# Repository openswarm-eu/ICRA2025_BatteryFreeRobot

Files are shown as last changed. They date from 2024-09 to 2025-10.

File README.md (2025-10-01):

# ICRA2025_Battery-Free Robot CapBot 

## Abstract

> Swarm robotics focuses on designing and coordinating large groups of relatively simple robots to perform tasks in a decentralised and collective manner.
> The swarm provides a resilient and flexible solution for many applications.
> However, contemporary swarm robots have a significant power problem in that secondary (i.e. rechargeable) batteries are slow to charge and offer lifetimes of only a few years, increasing maintenance costs and pollution due to battery replacement.
> We imagine a different future, wherein battery-free robots powered by supercapacitors can be recharged in seconds, offer long-life autonomous operation and can rapidly pass charge between one another using trophallaxis.
> In pursuit of this vision, we contribute the _CapBot_, a battery-free swarm robot equipped with Mecanum wheels, a Cortex-M4F application processor and Bluetooth Low Energy networking.
> CapBot  fully recharges in 16 s, offers 51 min of autonomous operation at top speed, and can transfer up to 50% of its available charge to a peer via trophallaxis in under 20 s.
> It is fully open-source: all software and hardware sources are available in this repository.

## Artefacts

### Hardware

CapBot's hardware is designed using KiCad, the design files are provided under [Hardware_Design](./Hardware_Design).

### Software

The [Software_Design](./Software_Design) folder contains an example using the CapBot Zephyr API.
The library itself is hosted at our [GitLab instance](https://gitlab.kuleuven.be/distrinet/taskforces/nes/capbot) and is included in this example using git submodules.

# CapBot ICRA demo

Fetch submodules:
```sh
git submodule update --init
```
Open workspace in [Visual Studio Code](https://code.visualstudio.com/):
```sh
code Software_Design
```
Make sure that the nRF Connect extension is installed according to the instructions at [Nordic's DevAcademy](https://academy.nordicsemi.com/courses/nrf-connect-sdk-fundamentals/lessons/lesson-1-nrf-connect-sdk-introduction/topic/exercise-1-1/)
Now, you should be able to open an nRF Connect terminal in Visual Studio Code. 
Next, execute [west](https://docs.nordicsemi.com/bundle/ncs-latest/page/zephyr/develop/west/index.html):
```sh
west build --build-dir build --board freebot-nrf52840 . -- -DBOARD_ROOT=.
```
This builds the demo project and creates a binary at `build/zephyr/zephyr.elf`.
[PyOCD](https://pyocd.io/) can then be used to flash the binary to the robot:
```sh
pyocd load -t nrf52840 build/zephyr/zephyr.hex
```

# Acknowledgement

Part of the source code in this repository is developed within the frame and for the purpose of the OpenSwarm project. This project has received funding from the European Unioan's Horizon Europe Framework Programme under Grant Agreement No. 101093046.

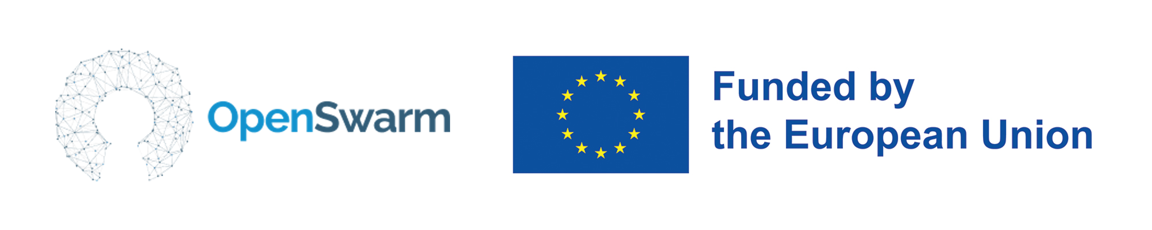
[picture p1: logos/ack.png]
OpenSwarm - Funded by the European Union


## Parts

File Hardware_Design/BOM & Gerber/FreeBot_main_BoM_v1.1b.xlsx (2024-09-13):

FreeBot_BoM
Source: | /Users/fan/work/projects/NetBot/FreeBot/FreeBot_v1.1/FreeBot_main/FreeBot_main_v1.1.kicad_sch
Date: | 2024 March 30, Tuesday 18:43:59
Tool: | Eeschema 7.0.5-0
Generator: | /Applications/KiCad/KiCad.app/Contents/SharedSupport/plugins/bom_csv_grouped_by_value_with_fp.py
Component Count: | 133
Ref | Qnty | Value | Part Nr | Footprint | Description | Vendor
A2 | 0 | DNP | Board layout | Arduino Nano
A3 | 0 | DNP | Board layout | Adafruit Feather
BT1 | 0 | DNP | Battery_Cell | Battery:BatteryHolder_Keystone_1058_1x2032 | Single-cell battery
C1, C24, C32, C33, C37 | 5 | 10uF | C | Capacitor_SMD:C_0603_1608Metric | Unpolarized capacitor
C2, C25, C38 | 3 | 10pF | C | Capacitor_SMD:C_0402_1005Metric | Unpolarized capacitor
C3, C4, C5, C20 | 4 | 1uF | C | Capacitor_SMD:C_0402_1005Metric | Unpolarized capacitor
C6, C8 | 2 | 22p | C | Capacitor_SMD:C_0402_1005Metric | Unpolarized capacitor
C7, C9, C10, C11, C12, C21, C22, C23, C29, C34, C35, C36 | 12 | 0.1uF | C | Capacitor_SMD:C_0402_1005Metric | Unpolarized capacitor
C13, C14, C17, C18, C26, C27, C39, C40 | 8 | 22uF | C | Capacitor_SMD:C_0603_1608Metric | Unpolarized capacitor
C15, C16 | 2 | 12pF | C | Capacitor_SMD:C_0402_1005Metric | Unpolarized capacitor
C19 | 1 | 2.2uF | C | Capacitor_SMD:C_0402_1005Metric | Unpolarized capacitor
C28 | 1 | 0.01uF | C | Capacitor_SMD:C_0402_1005Metric | Unpolarized capacitor
C30 | 0 | DNP | C | Capacitor_SMD:C_0603_1608Metric | Unpolarized capacitor
C31 | 0 | DNP | C | Capacitor_SMD:C_0402_1005Metric | Unpolarized capacitor
D1 | 1 | LED Red | NCD0603R1 | LED_SMD:LED_0603_1608Metric | Light emitting diode
D2 | 1 | LED Green | NCD0603G1 | LED_SMD:LED_0603_1608Metric | Light emitting diode
D3, D6, D17 | 3 | CUS10S30,H3F | 1N4148WS | Diode_SMD:D_SOD-323 | 75V 0.15A Fast switching Diode, SOD-323
D4, D5 | 2 | Schottky Rectifier Low VF Low IR | 10S45SP | Package_TO_SOT_SMD:TO-277A | 600V 6.0A Ultrafast Rectifier, TO-277A
D7, D10, D11, D14 | 0 | DNP | LED | LED_SMD:LED_0603_1608Metric | Light emitting diode
D8, D9, D12, D13 | 0 | DNP | LED | LED_SMD:LED_0603_1608Metric | Light emitting diode
D15, D16 | 2 | LED Blue | 19-217/BHC-ZL1M2RY/3T | LED_SMD:LED_0603_1608Metric | Light emitting diode
F1 | 1 | 0467002.NRHF | Fuse | Fuse:Fuse_0603_1608Metric | Fuse
FID1, FID2 | 0 | DNP | Fiducial | Fiducial:Fiducial_1mm_Mask2mm | Fiducial Marker
H1, H2, H3, H4, H5, H6, H7, H8 | 0 | DNP | MountingHole | MountingHole:MountingHole_2.2mm_M2_ISO7380 | Mounting Hole without connection
H9, H10, H11, H12 | 0 | DNP | MountingHole | MountingHole:MountingHole_3.2mm_M3_ISO14580 | Mounting Hole without connection
J1 | 1 | USB TYPE-C 16P | NCD0603G1 | Fan-socket-connector:TYPE-C-31-M-12
J2, J18 | 0 | DNP | Conn_01x05 | Connector_PinHeader_2.54mm:PinHeader_1x05_P2.54mm_Vertical | Generic connector, single row, 01x05, script generated (kicad-library-utils/schlib/autogen/connector/)
J3 | 0 | DNP | Conn_01x04 | Connector_PinHeader_2.54mm:PinHeader_1x04_P2.54mm_Vertical | Generic connector, single row, 01x04, script generated (kicad-library-utils/schlib/autogen/connector/)
J4, J5 | 2 | ROUND SPACER STEEL 2MM | 9774020960R (国产替代） | ROUND SPACER STEEL 2MM | ROUND SPACER STEEL 2MM | https://item.taobao.com/item.htm?_u=t2dmg8j26111&id=614508475805&skuId=4918073876504
J6 | 1 | Barrel_Jack_MountingPin | Barrel_Jack_MountingPin | Connector_BarrelJack:BarrelJack_GCT_DCJ200-10-A_Horizontal | DC Barrel Jack with a mounting pin
J7, J8, J9, J10 | 4 | ZH 1x6p1.5mm | ZH 1.5-6A | Fan-Connectors:ZH-1.5mm-1x6p-TH | Generic connector, single row, 01x06, script generated (kicad-library-utils/schlib/autogen/connector/)
J11 | 0 | DNP | Conn_01x07 | Connector_PinHeader_2.00mm:PinHeader_1x07_P2.00mm_Vertical | Generic connector, single row, 01x07, script generated (kicad-library-utils/schlib/autogen/connector/)
J12 | 0 | DNP | Conn_02x08_Odd_Even | Connector_PinHeader_2.54mm:PinHeader_2x08_P2.54mm_Horizontal | Generic connector, double row, 02x08, odd/even pin numbering scheme (row 1 odd numbers, row 2 even numbers), script generated (kicad-library-utils/schlib/autogen/connector/)
J13 | 0 | DNP | Conn_01x06 | Connector_PinHeader_2.54mm:PinHeader_1x06_P2.54mm_Vertical_SMD_Pin1Right
J14, J16 | 2 | DZ-32 | Conn_01x01 | Fan-Connectors:M3-side-terminal-DZ-32 | Generic connector, single row, 01x01, script generated (kicad-library-utils/schlib/autogen/connector/) | https://item.taobao.com/item.htm?_u=u2im4ruf08aa&id=528747753236&skuId=4568652374504
J15, J17 | 2 | DZ-43 | Conn_01x01 | Fan-Connectors:M3-side-terminal-DZ-43 | Generic connector, single row, 01x01, script generated (kicad-library-utils/schlib/autogen/connector/) | https://item.taobao.com/item.htm?_u=u2im4ruf08aa&id=528747753236&skuId=4568652374504
J19 | 0 | DNP | Conn_01x02 | Connector_PinHeader_2.54mm:PinHeader_1x02_P2.54mm_Vertical | Generic connector, single row, 01x02, script generated (kicad-library-utils/schlib/autogen/connector/)
J21 | 1 | HDGC2001WR-S-2P | Conn_01x03 | Connector_JST:JST_PH_S2B-PH-SM4-TB_1x02-1MP_P2.00mm_Horizontal
J23, J24 | 0 | DNP | Conn_01x08 | Connector_PinHeader_2.54mm:PinHeader_1x08_P2.54mm_Vertical_SMD_Pin1Right
J25 | 0 | DNP | Conn_01x10 | Connector_PinHeader_2.54mm:PinHeader_1x10_P2.54mm_Vertical_SMD_Pin1Right
L1 | 1 | 300nH | FXL1040-R30-M | Inductor_SMD:L_Chilisin_BMRF00101040 | Inductor
L2, L3 | 2 | 470nH | FXL0420-R47-M | Inductor_SMD:L_Sunlord_MWSA0412S | Inductor
L4 | 1 | 1uH | FXL0630-1R0-M | Inductor_SMD:L_Sunlord_MWSA0603S | Inductor
R1, R2 | 2 | 5.1k | R | Resistor_SMD:R_0402_1005Metric | Resistor
R3, R7, R18, R22, R27, R31, R32, R35, R36, R38, R40, R44, R45, R48, R68, R70 | 16 | 100k | R | Resistor_SMD:R_0402_1005Metric | Resistor
R4, R5, R6, R11, R12, R13, R14, R15, R16 | 9 | 22 | R | Resistor_SMD:R_0402_1005Metric | Resistor
R8, R29, R30, R33, R37, R41, R51, R52, R53, R54, R55, R56, R57, R58, R61, R65 | 0 | DNP | R | Resistor_SMD:R_0402_1005Metric | Resistor
R9, R20, R59, R60 | 4 | 100 | R | Resistor_SMD:R_0402_1005Metric | Resistor
R10, R62, R66 | 3 | 0 | R | Resistor_SMD:R_0402_1005Metric | Resistor
R17 | 1 | 1.5k | R | Resistor_SMD:R_0402_1005Metric | Resistor
R19 | 0 | DNP | R | Resistor_SMD:R_1206_3216Metric | Resistor
R21 | 1 | 27 | R | Resistor_SMD:R_0402_1005Metric | Resistor
R23, R25, R43, R47, R50 | 5 | 10k | R | Resistor_SMD:R_0402_1005Metric | Resistor
R24 | 1 | 36.5k | R | Resistor_SMD:R_0402_1005Metric | Resistor
R26, R67 | 2 | 1 | R | Resistor_SMD:R_0402_1005Metric | Resistor
R28 | 1 | 499k | R | Resistor_SMD:R_0402_1005Metric | Resistor
R34 | 1 | 348k | R | Resistor_SMD:R_0402_1005Metric | Resistor
R39 | 1 | 316k | R | Resistor_SMD:R_0402_1005Metric | Resistor
R42, R46, R49 | 3 | 390k | R | Resistor_SMD:R_0402_1005Metric | Resistor
R69 | 1 | 806k | R | Resistor_SMD:R_0402_1005Metric | Resistor
R63, R64 | 0 | DNP | R | Resistor_SMD:R_0805_2012Metric_Pad1.20x1.40mm_HandSolder | Resistor
SW1, SW2 | 2 | SW_Push | TS-1088-AR02016 | Button_Switch_SMD:SW_Push_SPST_NO_Alps_SKRK | Push button switch, generic, two pins
SW3 | 0 | DNP | Switch-4PDT | Fan-switch:4PDT-K3-2268S-F1
SW4 | 0 | DNP | Switch-DPDT | Fan-switch:DPDT-K3-2235S-F1
U1, U11 | 2 | Boost DCDC | TPS61021ADSGR | Package_SON:WSON-8-1EP_2x2mm_P0.5mm_EP0.9x1.6mm_ThermalVias
U2 | 1 | SPDT analog switch | TS5A23159DGSR | Package_SO:VSSOP-10_3x3mm_P0.5mm | Dual SPDT 1ohm Bidirectional Analog Switch with Off protection, VSSOP-10
U3 | 1 | STM32F103CBTx | STM32F103CBT6 | Package_QFP:LQFP-48_7x7mm_P0.5mm | STMicroelectronics Arm Cortex-M3 MCU, 128KB flash, 20KB RAM, 72 MHz, 2.0-3.6V, 37 GPIO, LQFP48
U4, U5, U6, U7 | 4 | Motor-driver-1ch | BDR6120H | Fan-Motor:motor-driver-BDR6120H
U8 | 1 | Buck SIC431 | SIC431BED-T1-GE3 | Fan-pwr:MLP44-24L SiC431
U9 | 1 | RF Module | E73-2G4M08S1C | Fan-MCU-Library:E73-2G4M08S1C
U10, U17 | 0 | DNP | TS5A23159DGSR | Package_SO:VSSOP-10_3x3mm_P0.5mm | Dual SPDT 1ohm Bidirectional Analog Switch with Off protection, VSSOP-10
U12 | 0 | DNP | RT9742AGJ5F | Package_TO_SOT_SMD:TSOT-23-5 | 3A, Discharge, Active High EN, TSOT-23-5
U13 | 1 | 100mA Voltage Regulator | HT7536-1 | Package_TO_SOT_SMD:SOT-89-3 | 100mA Low Dropout Voltage Regulator, Fixed Output, SOT89
U14 | 1 | Boost DCDC | TPS61022RWUR | VQFN7_2x2 | 8-A boost converter with 0.5-V ultra-low input voltage in a VQFN-HR (RWU) package with 7 pins.
U15 | 1 | TS3A27518EPWR | TS3A27518EPW | Package_SO:TSSOP-24_4.4x7.8mm_P0.65mm | 6-channel analog mux, TSSOP-24
Y1 | 1 | Crystal_GND24 | X32258MSB4SI | Crystal:Crystal_SMD_3225-4Pin_3.2x2.5mm | Crystal 8MHz
Y2 | 1 | Crystal | Q13FC1350000400 | Crystal:Crystal_SMD_3215-2Pin_3.2x1.5mm | Crystal 32.768kHz | Q13FC1350000400

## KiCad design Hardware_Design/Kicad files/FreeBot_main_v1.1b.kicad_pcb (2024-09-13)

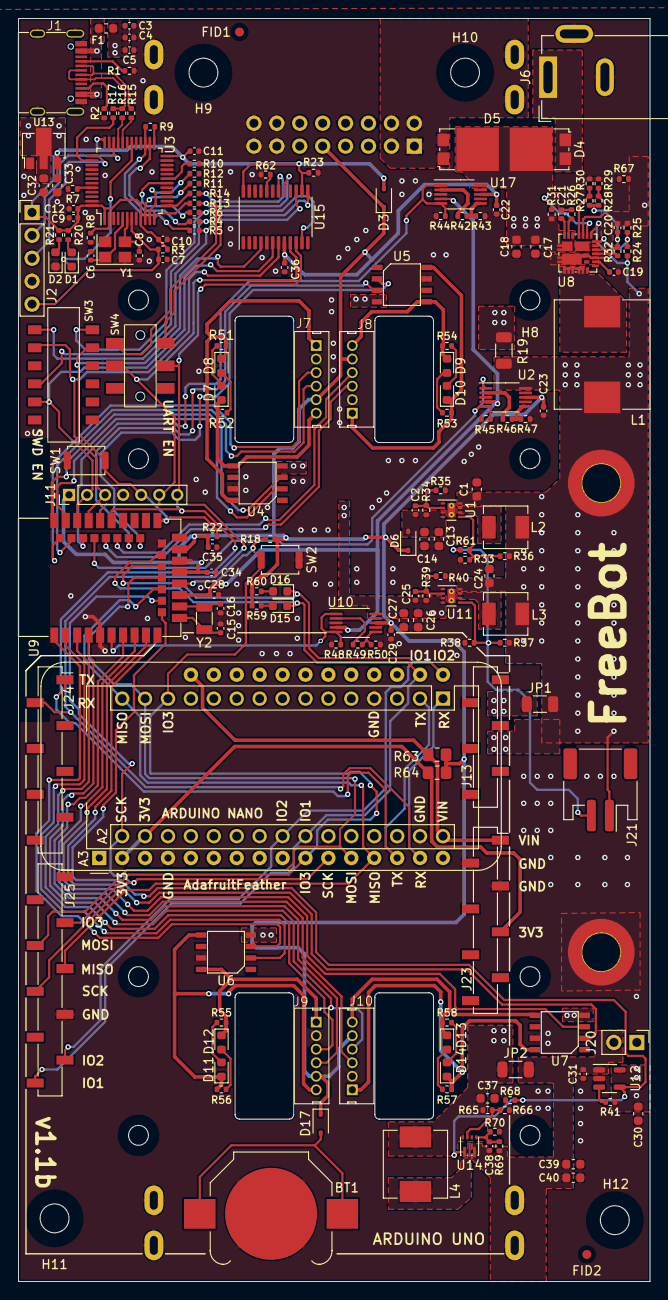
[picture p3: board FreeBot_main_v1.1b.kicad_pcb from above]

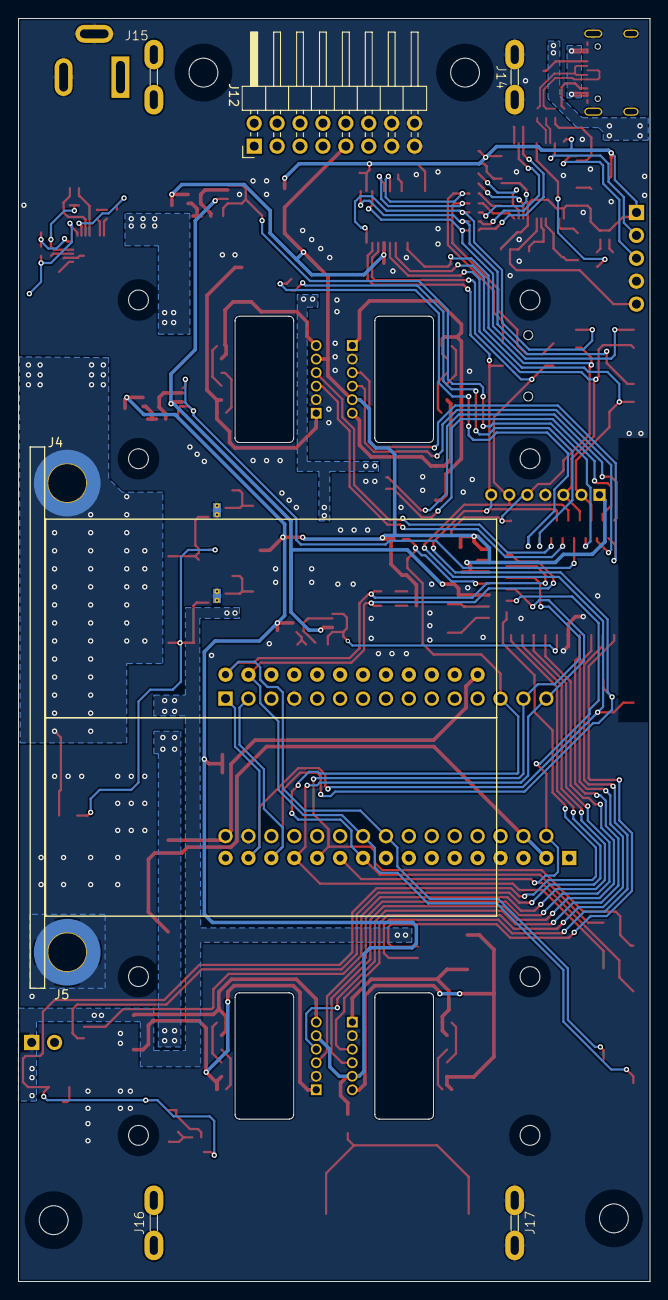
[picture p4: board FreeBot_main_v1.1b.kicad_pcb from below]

Board: 2 copper layers, 70.0 x 140.0 mm, 194 parts (7 on the bottom side), 126 nets.

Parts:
A2: Arduino_Nano_v3.x; Arduino_Nano
A3: Adafruit_Feather_Generic; Adafruit_Feather
BT1: Battery_Cell; BatteryHolder_Keystone_3000_1x12mm
C1, C24, C30, C32, C33, C37: 10uF; C_0603_1608Metric
C2, C25, C38: 10pF; C_0402_1005Metric
C3, C4, C5, C20: 1uF; C_0402_1005Metric
C6, C8: 22p; C_0402_1005Metric
C7, C9, C10, C11, C12, C21, C22, C23, C29, C31, C34, C35, C36: 0.1uF; C_0402_1005Metric
C13, C14, C17, C18, C26, C27, C39, C40: 22uF; C_0603_1608Metric
C15, C16: 12pF; C_0402_1005Metric
C19: 2.2uF; C_0402_1005Metric
C28: 0.01uF; C_0402_1005Metric
D1: Red; LED_0603_1608Metric
D2: Green; LED_0603_1608Metric
D3, D6, D17: CUS10S30,H3F; D_SOD-323
D4, D5: 10S45SP; TO-277A
D7, D10, D11, D14: GREEN LED NCD0603G1; LED_0603_1608Metric
D8, D9, D12, D13: RED LED NCD0603R1; LED_0603_1608Metric
D15, D16: 19-217/BHC-ZL1M2RY/3T; LED_0603_1608Metric
F1: S1206-F-6.0A; Fuse_0603_1608Metric
FID1, FID2: Fiducial; Fiducial_1mm_Mask2mm
H1, H2, H3, H4, H5, H6, H7, H8: MountingHole; MountingHole_2.2mm_M2_ISO7380
H9, H10, H11, H12: MountingHole; MountingHole_3.2mm_M3_ISO14580
J1: USB-type-c-16p; TYPE-C-31-M-12
J2: Conn_01x05; PinHeader_1x05_P2.54mm_Vertical
J4, J5: Conn_01x01; MountingHole_3.2mm_M3_Pad_TopBottom
J6: Barrel_Jack_MountingPin; BarrelJack_GCT_DCJ200-10-A_Horizontal
J7, J8, J9, J10: Conn_01x06; ZH-1.5mm-1x6p-TH
J11: Conn_01x07; PinHeader_1x07_P2.00mm_Vertical
J12: Conn_02x08_Odd_Even; PinHeader_2x08_P2.54mm_Horizontal
J13: Conn_01x06; PinSocket_1x06_P2.54mm_Vertical_SMD_Pin1Right
J14, J16: Conn_01x01; M3-side-terminal-DZ-32
J15, J17: Conn_01x01; M3-side-terminal-DZ-43
J20: Conn_01x02; PinHeader_1x02_P2.54mm_Vertical
J21: Conn_01x02; JST_PH_S2B-PH-SM4-TB_1x02-1MP_P2.00mm_Horizontal
J23, J24: Conn_01x08; PinSocket_1x08_P2.54mm_Vertical_SMD_Pin1Right
J25: Conn_01x10; PinSocket_1x10_P2.54mm_Vertical_SMD_Pin1Right
JP1, JP2: SolderJumper_2_Open; R_1206_3216Metric
L1: 300nH; L_Chilisin_BMRF00101040
L2, L3: 470nH FXL0420-R47-M; L_Sunlord_MWSA0412S
L4: 1uH FXL0630-1R0-M; L_Sunlord_MWSA0603S
R1, R2: 5.1k; R_0402_1005Metric
R3, R7, R18, R22, R27, R31, R32, R35, R36, R38, R40, R41, R44, R45, R48, R68, R70: 100k; R_0402_1005Metric
R4, R5, R6, R11, R12, R13, R14, R15, R16: 22; R_0402_1005Metric
R8: 10k DNP; R_0402_1005Metric
R9, R20, R52, R53, R56, R57, R59, R60: 100; R_0402_1005Metric
R10, R62, R66: 0; R_0402_1005Metric
R17: 1.5k; R_0402_1005Metric
R19: DNP; R_1206_3216Metric
R21, R51, R54, R55, R58: 27; R_0402_1005Metric
R23, R25, R43, R47, R50: 10k; R_0402_1005Metric
R24: 36.5k; R_0402_1005Metric
R26, R67: 1; R_0402_1005Metric
R28: 499k; R_0402_1005Metric
R29, R30, R33, R37, R61, R65: DNP; R_0402_1005Metric
R34: 348k; R_0402_1005Metric
R39: 316k; R_0402_1005Metric
R42, R46, R49: 390k; R_0402_1005Metric
R63, R64: R; R_0805_2012Metric_Pad1.20x1.40mm_HandSolder
R69: 806k; R_0402_1005Metric
SW1, SW2: TS-1088-AR02016; SW_Push_SPST_NO_Alps_SKRK
SW3: 4PDT-K3-2268S-F1
SW4: Switch-DPDT; DPDT-K3-2235S-F1
U1, U11: WSON-8-1EP_2x2mm_P0.5mm_EP0.9x1.6mm_ThermalVias
U2, U10, U17: TS5A23159DGS; VSSOP-10_3x3mm_P0.5mm
U3: STM32F103CBTx; LQFP-48_7x7mm_P0.5mm
U4, U5, U6, U7: BDR6120H; motor-driver-BDR6120H
U8: SIC431AED-T1-GE3; MLP44-24L SiC431
U9: E73-2G4M08S1C
U12: RT9742AGJ5F; TSOT-23-5
U13: HT7536-1; SOT-89-3
U14: boost-TPS61022; VQFN-HR-7 TPS61022
U15: TS3A27518EPW; TSSOP-24_4.4x7.8mm_P0.65mm
Y1: Crystal_GND24; Crystal_SMD_3225-4Pin_3.2x2.5mm
Y2: Q13FC1350000400; Crystal_SMD_3215-2Pin_3.2x1.5mm

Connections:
/USB-VDD: C9.1, C10.1, C11.1, C12.1, C33.1, D3.2 (A), J2.1, R3.2, R20.1, R21.1, R23.1, U3.1 (VBAT), U3.9 (VDDA), U3.24 (VDD), U3.36 (VDD), U3.48 (VDD), U13.3 (VOUT), U15.14 (IN2), U15.24 (IN1)
/Vbotin: D5.1 (A), D5.2 (A), J12.1, J12.2, J12.3, J12.4, J15.1
/Vbotout: C31.2, C38.2, C39.1, C40.1, J16.1, J20.2, JP2.2 (B), R69.1, U12.1 (VOUT), U14.3 (VOUT)
/Vmotor: C25.2, C26.1, C27.1, C30.1, J20.1, JP1.2 (B), R39.1, R41.1, U4.4 (VDD), U5.4 (VDD), U6.4 (VDD), U7.4 (VDD), U10.10, U11.3 (VOUT), U11.4 (VOUT), U12.5 (VIN)
/add-on-board/3V3: A2.17 (3V3), A3.2 (3V3), J23.5, R64.2
/add-on-board/VIN: A2.30 (VIN), A3.28 (VBAT), J23.1, R63.2
/add-on-board/addon-io.1: A2.24 (A5), A3.18 (SCL), D15.1 (K), J25.10, U9.22 (P0.07)
/add-on-board/addon-io.2: A2.23 (A4), A3.17 (SDA), D16.1 (K), J25.9, U9.20 (P0.12)
/add-on-board/addon-io.3: A2.13 (D10), A3.10 (A5), J25.3, R18.2, SW2.2, U9.17 (P1.09)
/add-on-board/addon-spi.miso: A2.15 (D12), A3.13 (MISO), J25.5, U9.16 (P0.08)
/add-on-board/addon-spi.mosi: A2.14 (D11), A3.12 (MOSI), J25.4, U9.18 (P0.04/AIN2)
/add-on-board/addon-spi.sck: A2.16 (D13), A3.11 (SCK), J25.6, U9.14 (P0.06)
/add-on-board/uart.rx: A2.1 (D1/TX), A3.15 (TX), J11.6, J24.2, SW4.5, U9.35 (P0.24), U15.9 (COM4)
/add-on-board/uart.tx: A2.2 (D0/RX), A3.14 (RX), J11.7, J24.1, SW4.2, U9.33 (P0.13), U15.10 (COM5)
/daplink/dap-inner-usb_N: R15.2, U3.32 (PA11)
/daplink/dap-inner-usb_P: R16.2, U3.33 (PA12)
/daplink/dap-led-red: D1.1 (K), U3.30 (PA9)
/daplink/dap-nrst: C7.1, J2.5, R3.1, U3.7 (NRST)
/daplink/dap-swclk: J2.3, U3.37 (PA14)
/daplink/dap-swdio: J2.2, U3.34 (PA13)
/daplink/dap-usbd_N: J1.A7 (DN1), J1.B7 (DN2), R15.1
/daplink/dap-usbd_P: J1.A6 (DP1), J1.B6 (DP2), R16.1, R17.2
/daplink/tgt-rx-dap: R13.2, SW4.4, U15.17 (NO4)
/daplink/tgt-swd-clk-dap: R4.1, SW3.10, U15.13 (NO2)
/daplink/tgt-swd-io-dap: R5.1, SW3.7, U15.15 (NO3)
/daplink/tgt-swd-rst-dap: R6.1, SW3.1, U15.11 (NO1)
/daplink/tgt-swd.clk: J11.2, SW3.11, U9.39 (SWDCLK), U15.6 (COM2)
/daplink/tgt-swd.io: J11.3, SW3.8, U9.37 (SWDIO), U15.7 (COM3)
/daplink/tgt-swd.rst: J11.5, R22.2, SW1.2, SW3.2, U9.26 (P0.18/RESET), U15.4 (COM1)
/daplink/tgt-tx-dap: R14.2, SW4.1, U15.18 (NO5)
/mcu/V-mea: C28.1, U2.4, U9.15 (P0.05/AIN3), U10.4, U17.4
/mcu/Vbotout-EN: R68.1, U9.12 (P0.26), U12.4 (EN), U14.1 (EN)
/mcu/Vcap-mea-en: R45.1, U2.1, U2.5, U9.36 (P1.00/SWO)
/mcu/Vin-mea-en: R44.1, U9.38 (P1.02-LS), U17.1, U17.5
/mcu/Vmotor-mea-en: R48.1, U9.6 (P1.13-LS), U10.1, U10.5
/mcu/m1-ctrl.in-a: U4.2 (INA), U9.41 (P0.09/NFC1-LS)
/mcu/m1-ctrl.in-b: U4.3 (INB), U9.43 (P0.10/NFC2-LS)
/mcu/m1-hall.c1: J7.4, U9.40 (P1.04-LS)
/mcu/m1-hall.c2: J7.3, U9.42 (P1.06-LS)
/mcu/m2-ctrl.in-a: U5.2 (INA), U9.28 (P0.15)
/mcu/m2-ctrl.in-b: U5.3 (INB), U9.30 (P0.17)
/mcu/m2-hall.c1: J8.4, U9.32 (P0.20)
/mcu/m2-hall.c2: J8.3, U9.34 (P0.22)
/mcu/m3-ctrl.in-a: U6.2 (INA), U9.2 (P1.10-LS)
/mcu/m3-ctrl.in-b: U6.3 (INB), U9.1 (P1.11-LS)
/mcu/m3-hall.c1: J9.4, U9.7 (P0.02/AIN1-LS)
/mcu/m3-hall.c2: J9.3, U9.3 (P0.03/AIN1-LS)
/mcu/m4-ctrl.in-a: U7.2 (INA), U9.10 (P0.30/AIN6-LS)
/mcu/m4-ctrl.in-b: U7.3 (INB), U9.9 (P0.31/AIN7-LS)
/mcu/m4-hall.c1: J10.4, U9.4 (P0.28/AIN4-LS)
/mcu/m4-hall.c2: J10.3, U9.8 (P0.29/AIN5-LS)
/pwr1/buck_en: R31.2, U8.19 (EN)
/pwr2/Vbotout-overcurr: R41.2, U12.3 (~FLG)
/pwr2/Vcap: C1.1, C24.1, C37.1, J4.1, J21.1, JP1.1 (A), JP2.1 (A), L1.2, L2.1, L3.1, L4.1, R19.2, R24.1, R36.1, R37.1, R65.1, U1.8 (VIN), U2.10, U8.18 (Vout), U11.8 (VIN), U14.7 (VIN)
/pwr2/Vcap_reg: C2.2, C13.1, C14.1, D6.2 (A), R34.1, U1.3 (VOUT), U1.4 (VOUT)
/pwr2/Vmotor-EN: J21.2, R37.2, R38.1, R61.2, U11.5 (EN)
GND: A2.4 (GND), A2.29 (GND), A3.4 (GND), BT1.2 (-), C1.2, C3.2, C4.2, C5.2, C6.2, C7.2, C8.2, C9.2, C10.2, C11.2, C12.2, C13.2, C14.2, C15.2, C16.2, C17.2, C18.2, C19.2, C20.2, C22.2, C23.2, C24.2, C26.2, C27.2, C28.2, C29.2, C30.2, C31.1, C32.2, C33.2, C34.2, C35.2, C36.1, C37.2, C39.2, C40.2, D2.1 (K), J1.0 (SH), J1.1 (SH), J1.2 (SH), J1.3 (SH), J1.A1 (GND), J1.A12 (GND), J1.B1 (GND), J1.B12 (GND), J2.4, J5.1, J6.2, J6.3 (MP), J7.2, J8.2, J9.2, J10.2, J11.4, J12.13, J12.14, J12.15, J12.16, J14.1, J17.1, J23.2, J23.3, J25.7, R1.2, R2.2, R7.2, R8.1, R10.1, R23.2, R25.2, R29.2, R30.2, R33.2, R35.2, R38.2, R40.2, R43.2, R44.2, R45.2, R47.2, R48.2, R50.2, R62.1, R66.2, R67.1, R67.2, R68.2, R70.2, SW1.1, SW2.1, U1.1 (AGND), U1.9 (PGND), U2.3 (GND), U3.8 (VSSA), U3.23 (VSS), U3.35 (VSS), U3.47 (VSS), U4.7 (GND), U5.7 (GND), U6.7 (GND), U7.7 (GND), U8.3 (Pgnd), U8.4 (Pgnd), U8.13 (Pgnd), U8.16 (Agnd), U8.25 (Agnd), U8.27 (Pgnd), U9.5 (GND), U9.21 (GND), U9.24 (GND), U10.3 (GND), U11.1 (AGND), U11.9 (PGND), U12.2 (GND), U13.1 (GND), U15.5 (GND), U17.3 (GND), Y1.2, Y1.4
unnamed: BT1.1 (+), D17.2 (A)
unnamed: C21.2, R26.2
unnamed: D1.2 (A), R20.2
unnamed: D2.2 (A), R21.2
unnamed: D4.1 (A), D4.2 (A), J6.1
unnamed: C17.1, C18.1, D4.3 (K), D5.3 (K), R19.1, R31.1, U8.1 (Vin), U8.2 (Vin), U8.22 (Vin), U8.26 (Vin), U17.10
unnamed: D7.2 (A), R51.2
unnamed: D7.1 (K), J7.6, R52.2, U4.5 (OUTB)
unnamed: D8.2 (A), R52.1
unnamed: D8.1 (K), J7.1, R51.1, U4.8 (OUTA)
unnamed: D9.2 (A), R53.2
unnamed: D9.1 (K), J8.6, R54.2, U5.5 (OUTB)
unnamed: D10.2 (A), R54.1
unnamed: D10.1 (K), J8.1, R53.1, U5.8 (OUTA)
unnamed: D11.2 (A), R55.2
unnamed: D11.1 (K), J9.6, R56.2, U6.5 (OUTB)
unnamed: D12.2 (A), R56.1
unnamed: D12.1 (K), J9.1, R55.1, U6.8 (OUTA)
unnamed: D13.2 (A), R57.2
unnamed: D13.1 (K), J10.6, R58.2, U7.5 (OUTB)
unnamed: D14.2 (A), R58.1
unnamed: D14.1 (K), J10.1, R57.1, U7.8 (OUTA)
unnamed: D15.2 (A), R59.2
unnamed: D16.2 (A), R60.2
unnamed: F1.1, J1.A4 (VBUS), J1.A9 (VBUS), J1.B4 (VBUS), J1.B9 (VBUS)
unnamed: J1.A5 (CC1), R1.1
unnamed: J1.B5 (CC2), R2.1
unnamed: L1.1, U8.5 (SW), U8.6 (SW), U8.7 (SW), U8.8 (SW), U8.9 (SW)
unnamed: L2.2, U1.6 (SW), U1.7 (SW)
unnamed: L3.2, U11.6 (SW), U11.7 (SW)
unnamed: R42.1, U17.2
unnamed: R42.2, R43.1, U17.6
unnamed: R46.1, U2.2
unnamed: R46.2, R47.1, U2.6
unnamed: R49.1, U10.2
unnamed: R49.2, R50.1, U10.6
unnamed: R33.1, R36.2, R61.1, U1.5 (EN)
unnamed: C2.1, R34.2, R35.1, U1.2 (FB)
unnamed: R7.1, U3.44 (BOOT0)
unnamed: R11.1, U3.10 (PA0)
unnamed: R12.1, U3.11 (PA1)
unnamed: R13.1, U3.12 (PA2)
unnamed: R14.1, U3.13 (PA3)
unnamed: R17.1, U3.38 (PA15)
unnamed: R6.2, U3.18 (PB0)
unnamed: R10.2, U3.19 (PB1)
unnamed: R9.2, U3.25 (PB12)
unnamed: R4.2, U3.26 (PB13)
unnamed: R5.2, R9.1, U3.27 (PB14)
unnamed: R8.2, U3.2 (PC13)
unnamed: C6.1, U3.5 (PD0), Y1.1
unnamed: C8.1, U3.6 (PD1), Y1.3
unnamed: R26.1, U8.23 (BOOT)
unnamed: R24.2, R25.1, U8.17 (FB)
unnamed: R27.2, R30.1, U8.21 (MODE1)
unnamed: R28.2, R29.1, U8.20 (MODE2)
unnamed: C21.1, U8.24 (PHASE)
unnamed: R32.2, U8.14 (Pgood)
unnamed: C20.1, R27.1, R28.1, R32.1, U8.15 (Vdd)
unnamed: C19.1, U8.12 (Vdrv)
unnamed: C15.1, U9.11 (P0.00/XL1), Y2.1
unnamed: C16.1, U9.13 (P0.01/XL2), Y2.2
unnamed: C25.1, R39.2, R40.1, U11.2 (FB)
unnamed: C38.1, R69.2, R70.1, U14.4 (FB)
unnamed: R65.2, R66.1, U14.6 (MODE)
unnamed: L4.2, U14.2 (SW)
unnamed: R62.2, U15.20 (~EN)
VBUS: C3.1, C4.1, C5.1, C32.1, F1.2, U13.2 (VIN)
VDD: C22.1, C23.1, C29.1, C34.1, C35.1, C36.2, D3.1 (K), D6.1 (K), D17.1 (K), J7.5, J8.5, J9.5, J10.5, J11.1, J12.9, R18.1, R22.1, R59.1, R60.1, R63.1, R64.1, U2.8 (VCC), U9.19 (VDD), U9.23 (VDDH), U10.8 (VCC), U15.8 (VCC), U17.8 (VCC)

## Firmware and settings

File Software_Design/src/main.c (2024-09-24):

/**
 * @file main.c
 * @author Lowie Deferme <lowie.deferme@kuleuven.be>
 * @brief FreeBot zephyr example
 * @version 0.1
 * @date 2024-09-22
 *
 * @copyright Copyright (c) 2024
 *
 */

#include <zephyr/kernel.h>
#include <zephyr/logging/log.h>

LOG_MODULE_REGISTER(demo, LOG_LEVEL_DBG);

#include "freebot.h"
#define FB_DEMO_DELAY K_MSEC(500)
#define FB_DEMO_SPEED 75

static fb_motor_angle_t motor_angles;
static fb_motor_speed_t motor_speeds;

void pwr_measure_demo(void)
{
    fb_v_measure_select(V_CAP);
    k_sleep(FB_DEMO_DELAY);
    int v_cap = fb_v_measure();
    LOG_DBG("Vcap = %dmV", v_cap);
}

void motor_drive_demo(void)
{
    fb_straight_forw(FB_DEMO_SPEED);
    LOG_DBG("Robot going forward");
    k_sleep(FB_DEMO_DELAY);

    fb_straight_back(FB_DEMO_SPEED);
    LOG_DBG("Robot going backward");
    k_sleep(FB_DEMO_DELAY);

    fb_side_right(FB_DEMO_SPEED);
    LOG_DBG("Robot going right");
    k_sleep(FB_DEMO_DELAY);

    fb_side_left(FB_DEMO_SPEED);
    LOG_DBG("Robot going left");
    k_sleep(FB_DEMO_DELAY);

    fb_side_d45(FB_DEMO_SPEED);
    LOG_DBG("Robot going 45°");
    k_sleep(FB_DEMO_DELAY);

    fb_side_d135(FB_DEMO_SPEED);
    LOG_DBG("Robot going 135°");
    k_sleep(FB_DEMO_DELAY);

    fb_side_d225(FB_DEMO_SPEED);
    LOG_DBG("Robot going 225°");
    k_sleep(FB_DEMO_DELAY);

    fb_side_d315(FB_DEMO_SPEED);
    LOG_DBG("Robot going 315°");
    k_sleep(FB_DEMO_DELAY);

    fb_rotate_cw(FB_DEMO_SPEED);
    LOG_DBG("Robot rotating clockwise");
    k_sleep(FB_DEMO_DELAY);

    fb_rotate_ccw(FB_DEMO_SPEED);
    LOG_DBG("Robot rotating counterclockwise");
    k_sleep(FB_DEMO_DELAY);

    fb_stop();
    LOG_DBG("Robot stopped");
}

void motor_measure_demo(void)
{
    fb_get_motor_angle(&motor_angles);
    LOG_DBG("{%d°, %d°, %d°, %d°}", motor_angles.front_left, motor_angles.front_right,
            motor_angles.back_left, motor_angles.back_right);

    fb_rotate_cw(FB_DEMO_SPEED);
    k_sleep(K_MSEC(200));
    fb_get_motor_speed(&motor_speeds);
    LOG_DBG("{%d rpm, %d rpm, %d rpm, %d rpm}", motor_speeds.front_left, motor_speeds.front_right,
            motor_speeds.back_left, motor_speeds.back_right);

    fb_stop();
    for (int i = 0; i < 4; i++)
    {
        k_sleep(K_MSEC(100));
        fb_get_motor_speed(&motor_speeds);
        LOG_DBG("{%d rpm, %d rpm, %d rpm, %d rpm}", motor_speeds.front_left,
                motor_speeds.front_right, motor_speeds.back_left, motor_speeds.back_right);
    }

    fb_get_motor_angle(&motor_angles);
    LOG_DBG("{%d°, %d°, %d°, %d°}", motor_angles.front_left, motor_angles.front_right,
            motor_angles.back_left, motor_angles.back_right);
}

void motor_speed_demo(void)
{
    const int STEPS = 10;
    for (int i = 0; i <= STEPS; i++)
    {
        fb_rotate_cw(100 * i / STEPS);
        LOG_DBG("Target speed: %d", 100 * i / STEPS);
        for (int j = 0; j < 10; j++)
        {
            k_sleep(K_MSEC(100));
            fb_get_motor_speed(&motor_speeds);
            LOG_DBG("{%d rpm, %d rpm, %d rpm, %d rpm}", motor_speeds.front_left,
                    motor_speeds.front_right, motor_speeds.back_left, motor_speeds.back_right);
        }
    }
    fb_stop();
}

int main(void)
{
    LOG_DBG("Starting Robot");
    fb_init();

    for (;;)
    {
        // Flash both leds in out of sync to indicate ready
        fb_set_led(D15);
        fb_clear_led(D16);

        for (;;)
        {
            k_sleep(K_MSEC(100));
            fb_toggle_led(D15);
            fb_toggle_led(D16);

            if (fb_read_btn())
            {
                LOG_DBG("Button pressed");
                break;
            }
        }

        // Turn both leds off during operation
        fb_clear_led(D15);
        fb_clear_led(D16);

        // Run demos
        pwr_measure_demo();
        motor_measure_demo();
        motor_drive_demo();
        motor_speed_demo();
    }
    return 0;
}

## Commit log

2024-09-13 Create Schematic
2024-09-13 Create KICAD project files
2024-09-24 Rename root folders
    [FreeBot_main_BoM_v1.1b.xlsx, FreeBot_main_v1.1b.kicad_pcb, FreeBot_main_v1.1b.kicad_sch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]
